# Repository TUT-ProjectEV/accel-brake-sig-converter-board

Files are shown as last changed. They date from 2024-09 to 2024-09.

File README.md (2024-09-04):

# accel-brake-sig-converter-board

## Revision
- v1.0

## Overview
- This board converts the sensor output VOLTAGE signal into the CURRENT signal
    - 4~20mA

## Requirement
### Development
- Kicad 8.0
### Libraries
- ProjectEV-Kicad-Library
    - v8.0

## Usage
- J1, J2, J3: Connect to Controller or ADC and Power supply
    - Pin 1: +12V Input
    - Pin 2: GND
    - Pin 3: Current Signal Output
- J4, J5, J6: Connect to Sensor
    - Pin 1: +5V Output
    - Pin 2: GND
    - Pin 3: Voltage Signal Input

## Features
- Input Signal Voltage Range: +1~+5V
- Output Signal Current Range: 4~20mA
    - 250 Ohms termination: +1~+5V

## Reference
- ["Reference Site Name"]("Reference URL")

## Author
- [ST04-tkmr](https://github.com/ST04-tkmr)

## License
- Copyright (c) 2024 東京工科大学 ProjectEV

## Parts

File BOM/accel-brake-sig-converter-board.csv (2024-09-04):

Reference | Value | Footprint | Qty | DNP | Mouser番号 | Package | digikey品番
C1 | 1000p | ProjectEV_Capacitor:C_3216M | 1 |  |  | 3216M
C2,C3,C4,C5,C6,C7,C8,C9,C10,C11,C12,C13 | 1u | ProjectEV_Capacitor:C_1608M | 12 |  |  | 1608M
C14,C15,C16 | 0.1u | ProjectEV_Capacitor:C_1608M | 3 |  |  | 1608M
C17,C18,C19 | 10n | ProjectEV_Capacitor:C_1608M | 3 | DNP |  | 1608M
D1,D2,D3 | PZ1AH11B-AU_R1_000A1 | ProjectEV_Diode:PZ1AH11B-AU_R1_000A1 | 3 |  | 241-PZ1AH11BAUR1000A
D4,D5,D6,D7,D8,D9 | B1911PG--20D000514U1930 | ProjectEV_LED:B1911PG--20D000514U1930 | 6 |  |  |  | 3147-B1911PG--20D000514U1930CT-ND
F1,F2,F3 | 0ABB-1000-TM | ProjectEV_Fuse:0ABB-1000-TM | 3 |  | 530-0ABB-1000-TM |  | 507-0ABB-5000-TMCT-ND
J1,J2,J3,J4,J5,J6 | SM03B-PASS-TBT | ProjectEV_Connector_JST:SM03B-PASS-TBT | 6 |  |  |  | 455-SM03B-PASS-TBTCT-ND
Q1,Q2,Q3 | DMP3098LQ-7 | ProjectEV_Transistor:DMP3098LQ-7 | 3 |  | 621-DMP3098LQ-7
Q4,Q5,Q6 | 2N7002K-AU_R1_000A2 | ProjectEV_Transistor:2N7002K-AU_R1_000A2 | 3 |  |  |  | 3757-2N7002K-AU_R1_000A2CT-ND
R1 | 1M | ProjectEV_Resistor:R_3216M | 1 |  |  | 3216M
R2,R3 | 0 | ProjectEV_Resistor:R_1608M | 2 |  |  | 1608M
R4,R5,R6,R13,R14,R15,R20,R22,R24,R26,R28,R30,R34,R35,R36 | 100k | ProjectEV_Resistor:R_1608M | 15 |  |  | 1608M
R7,R8,R9,R19,R21,R23,R25,R27,R29 | 10k | ProjectEV_Resistor:R_1608M | 9 |  |  | 1608M
R10,R11,R12 | 100 | ProjectEV_Resistor:R_1608M | 3 |  |  | 1608M
R16,R17,R18 | 3.3k | ProjectEV_Resistor:R_1608M | 3 |  |  | 1608M
R31,R32,R33 | RT1206BRC07250RL | ProjectEV_Resistor:RT1206BRC07250RL | 3 |  | 603-RT1206BRC07250RL | 3216M
U1,U2,U3 | NCV8711BMTW500TBG | ProjectEV_RegulatorLinear:NCV8711BMTW500TBG | 3 |  | 863-NCV8711BMTW500TB
U4,U5,U6 | NCV20072DR2G | ProjectEV_Opamp:NCV20072DR2G | 3 |  | 863-NCV20072DR2G

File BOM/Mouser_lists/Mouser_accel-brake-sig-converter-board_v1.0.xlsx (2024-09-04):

Reference | Manufacturer Part Number | Mouser Part Number | Description | Quantity 1 (実装個数) | Quantity 2
D1,D2,D3 | PZ1AH11B-AU_R1_000A1 | 241-PZ1AH11BAUR1000A |  | 3 | 6
F1,F2,F3 | 0ABB-1000-TM | 530-0ABB-1000-TM |  | 3 | 6
Q1,Q2,Q3 | DMP3098LQ-7 | 621-DMP3098LQ-7 |  | 3 | 6
R31,R32,R33 | RT1206BRC07250RL | 603-RT1206BRC07250RL |  | 3 | 6
U1,U2,U3 | NCV8711BMTW500TBG | 863-NCV8711BMTW500TB |  | 3 | 6

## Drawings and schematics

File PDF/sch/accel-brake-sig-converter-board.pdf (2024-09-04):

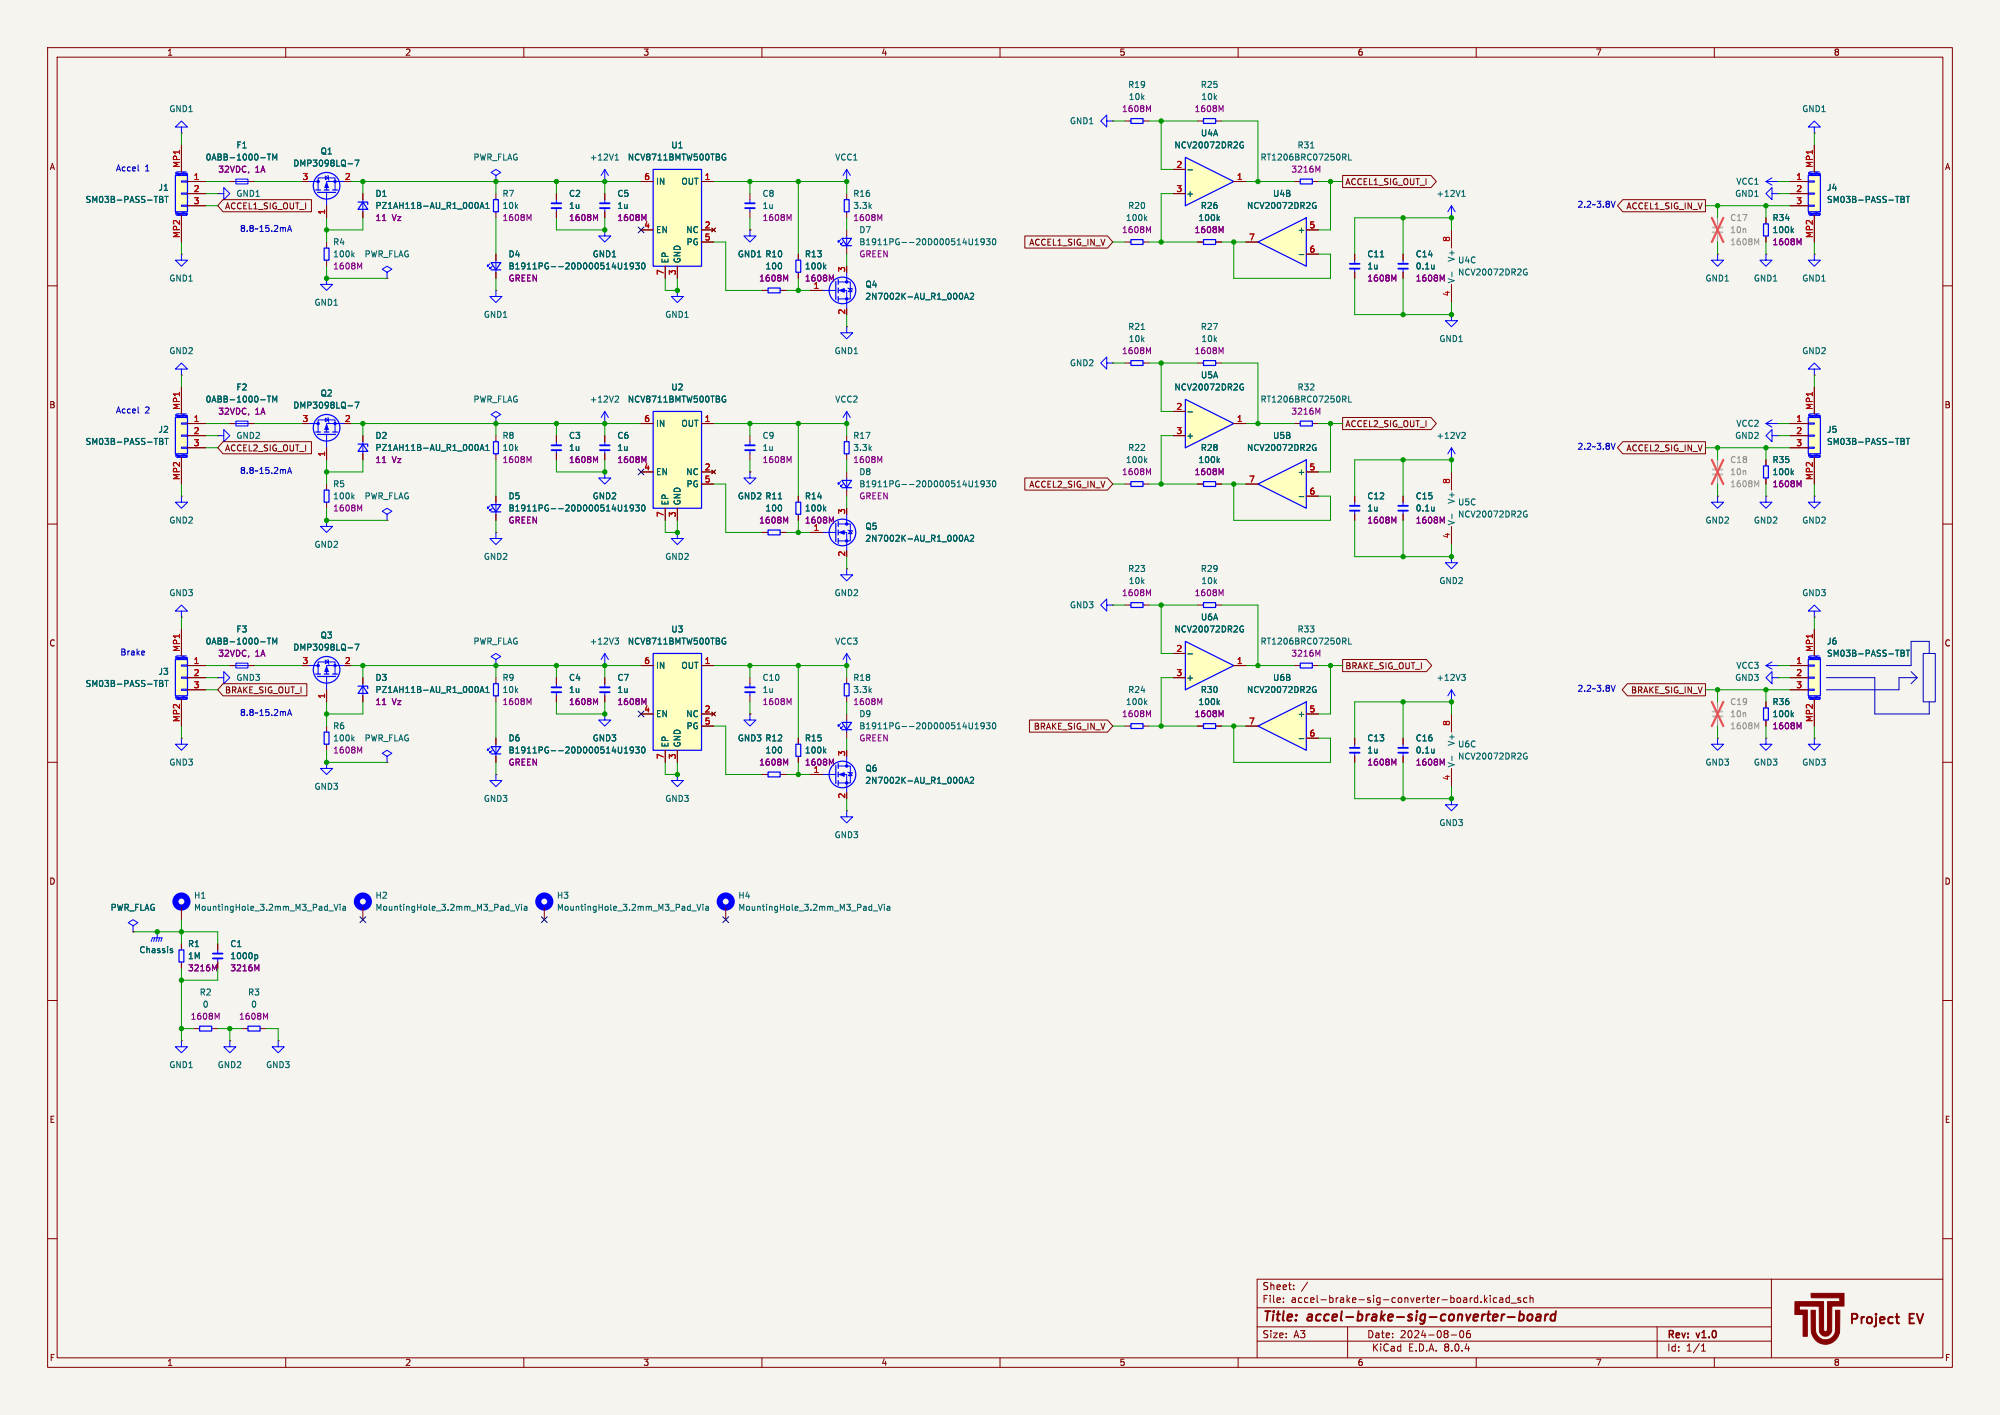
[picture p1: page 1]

Id: 1/1 Title: accel-brake-sig-converter-board

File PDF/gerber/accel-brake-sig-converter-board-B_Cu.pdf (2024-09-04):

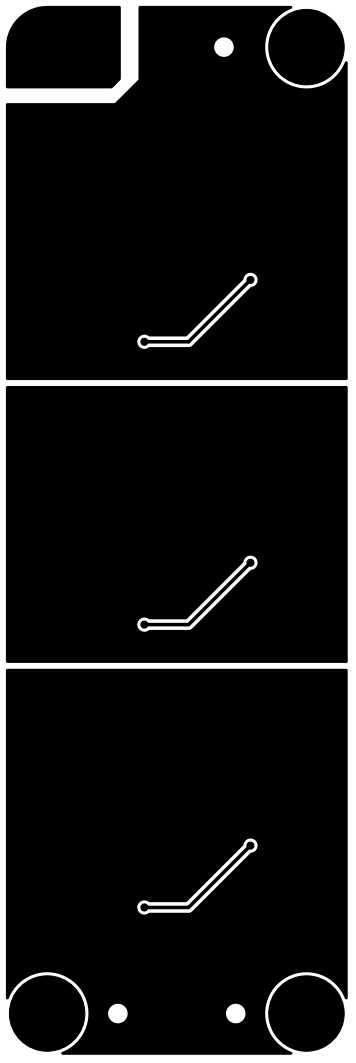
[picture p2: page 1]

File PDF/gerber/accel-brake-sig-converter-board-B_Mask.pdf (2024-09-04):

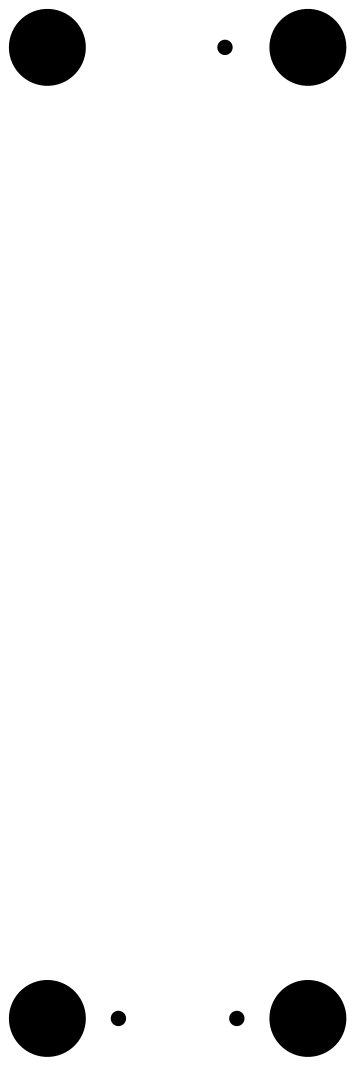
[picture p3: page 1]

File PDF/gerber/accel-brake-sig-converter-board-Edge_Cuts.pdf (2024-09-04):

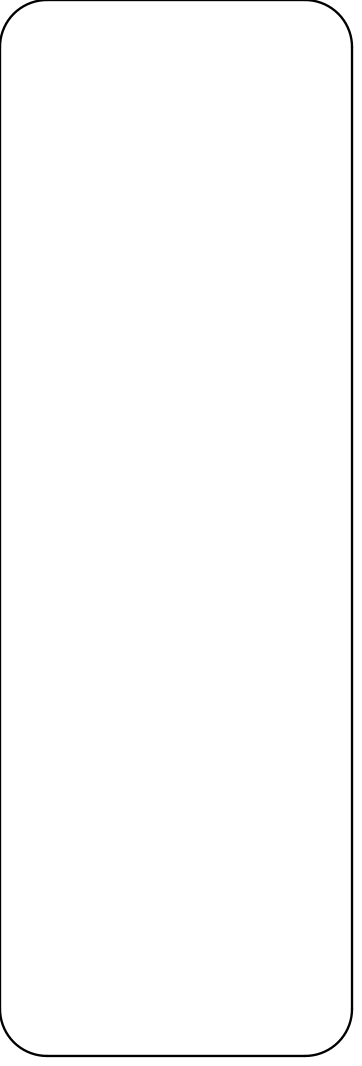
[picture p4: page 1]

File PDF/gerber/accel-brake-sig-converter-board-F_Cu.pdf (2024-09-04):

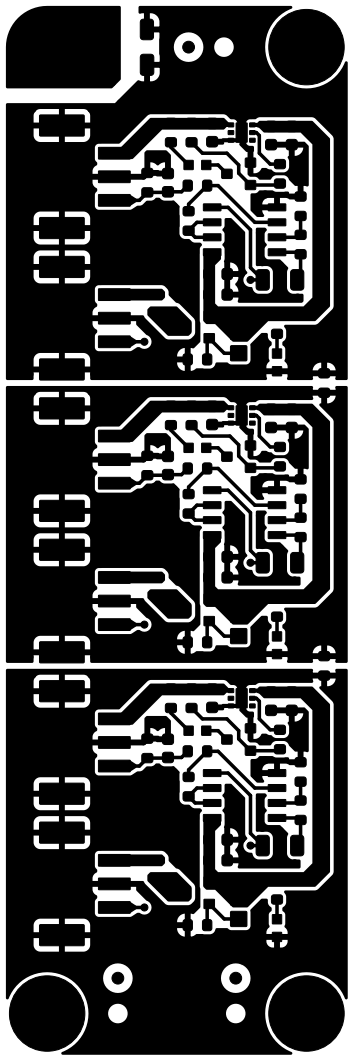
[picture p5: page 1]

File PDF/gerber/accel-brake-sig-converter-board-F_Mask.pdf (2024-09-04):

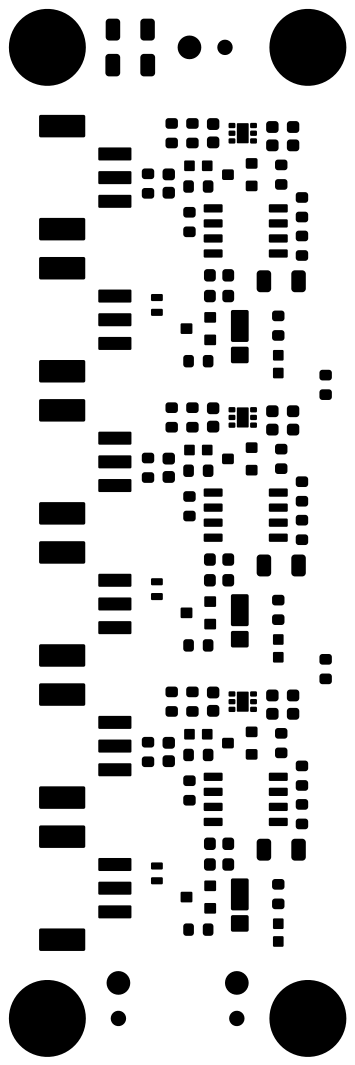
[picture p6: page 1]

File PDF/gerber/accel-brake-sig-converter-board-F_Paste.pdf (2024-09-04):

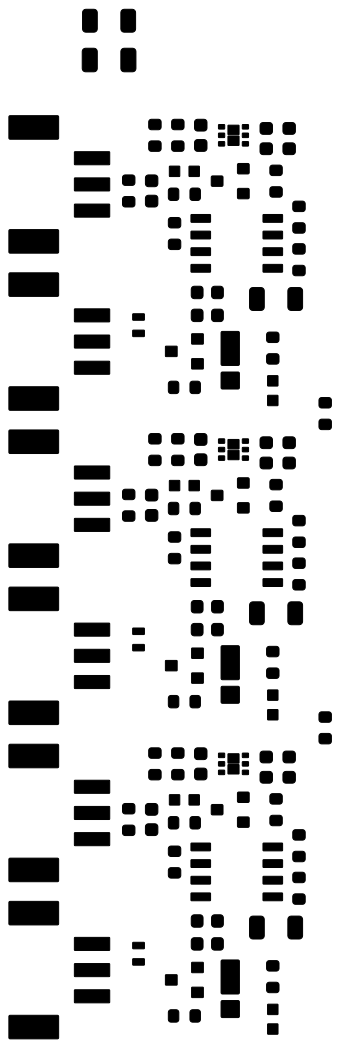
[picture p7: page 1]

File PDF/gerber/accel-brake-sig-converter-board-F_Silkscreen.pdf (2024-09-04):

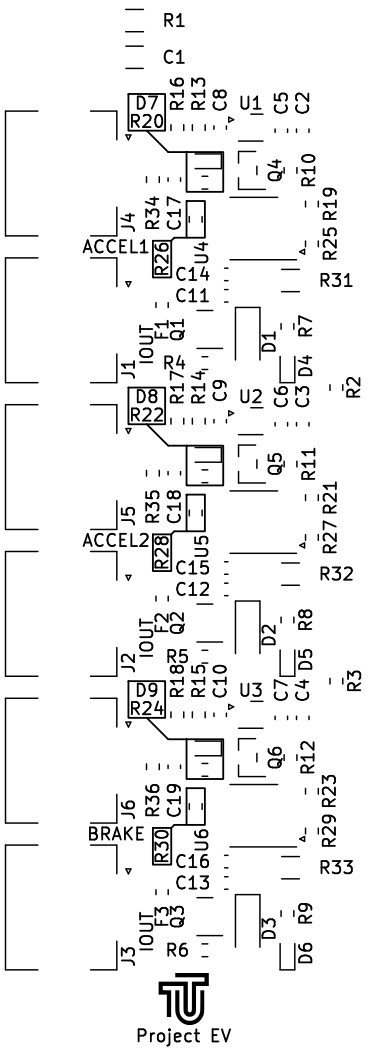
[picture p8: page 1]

IOUT IOUT Project EV

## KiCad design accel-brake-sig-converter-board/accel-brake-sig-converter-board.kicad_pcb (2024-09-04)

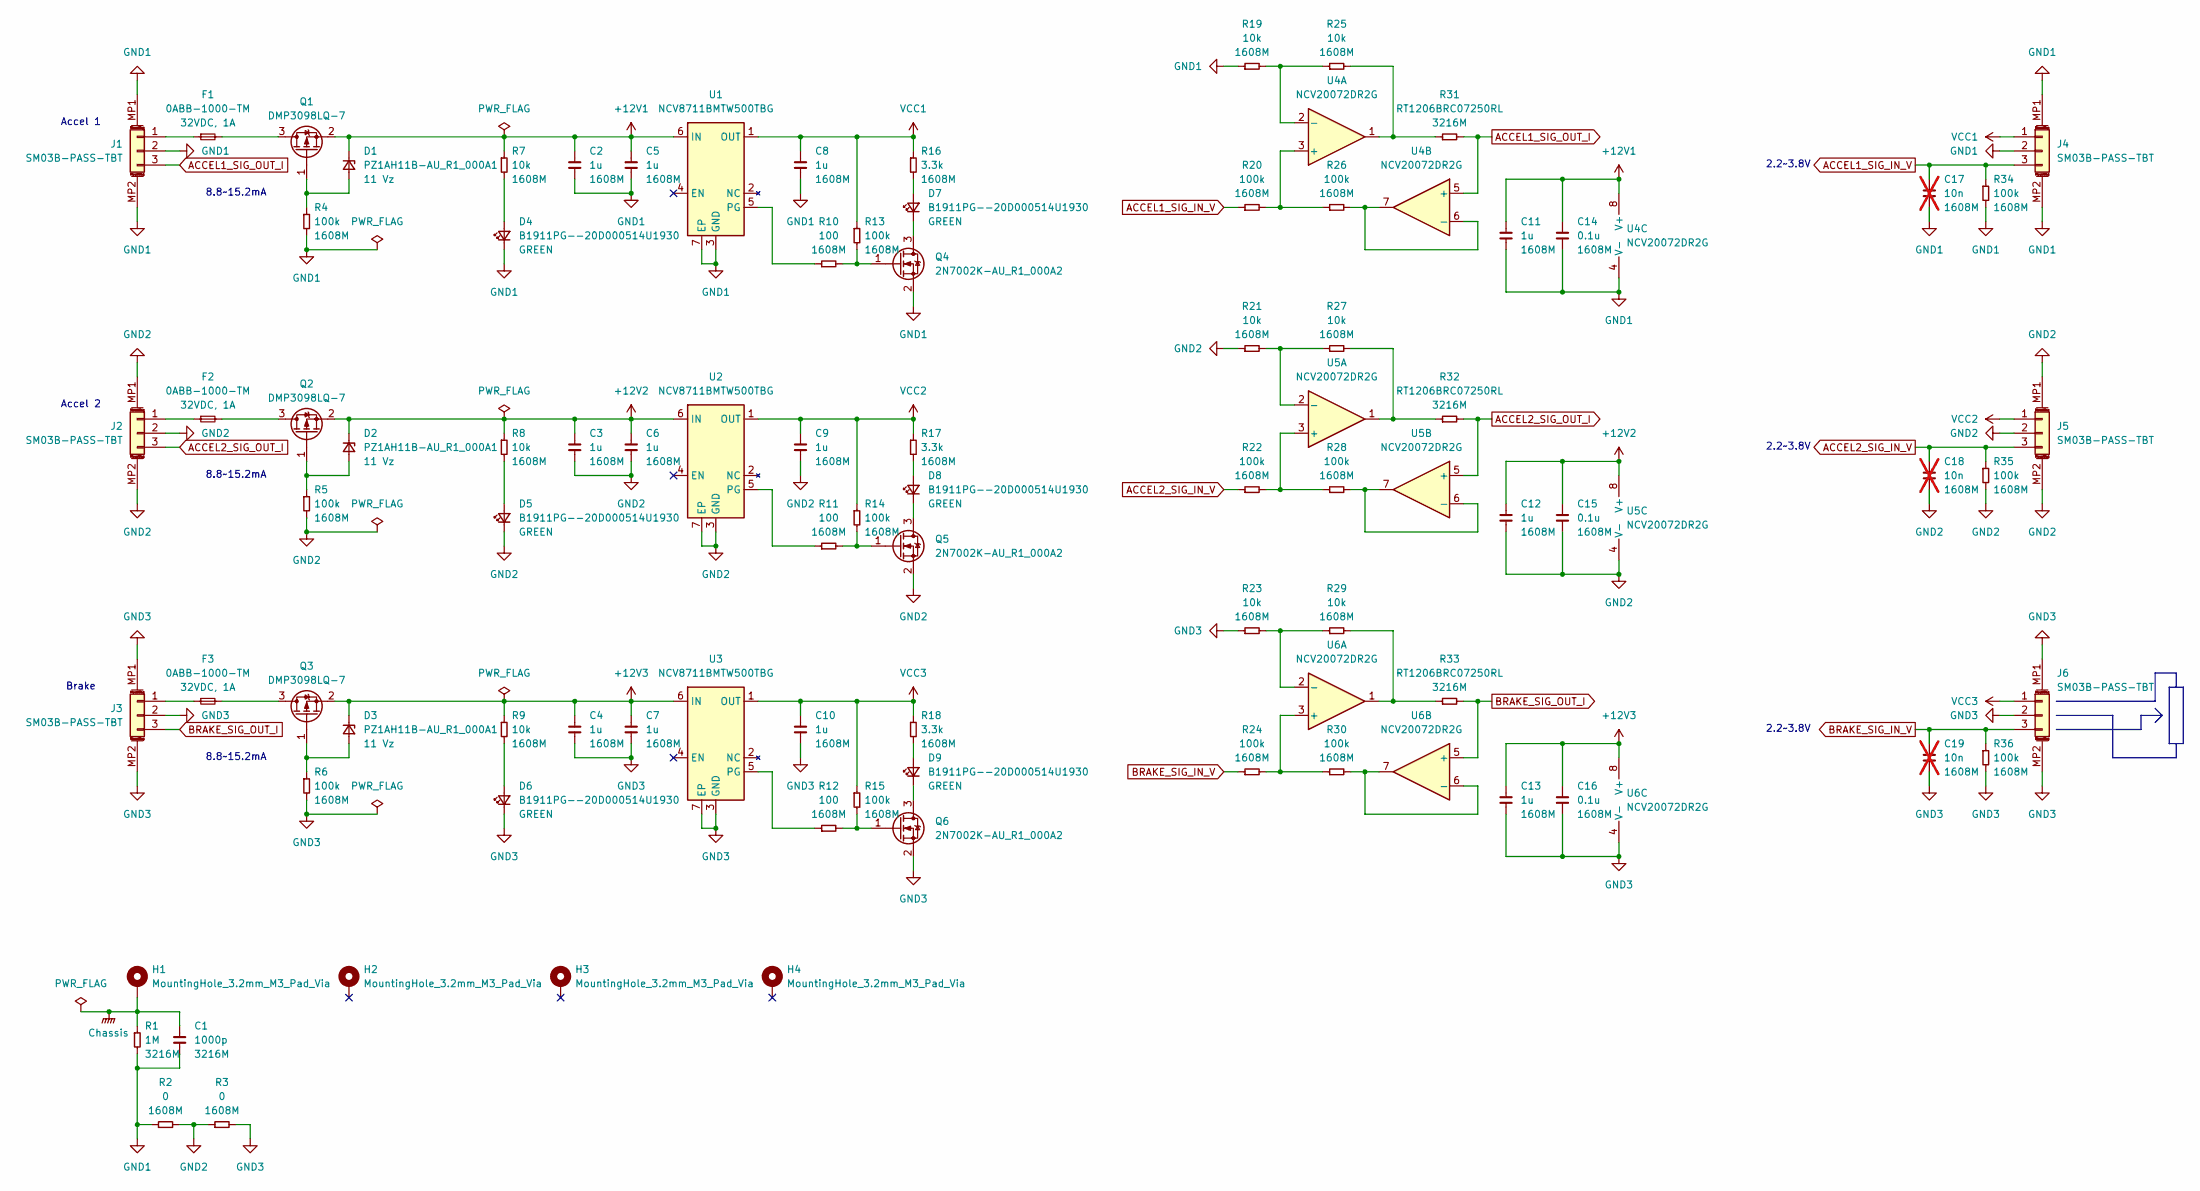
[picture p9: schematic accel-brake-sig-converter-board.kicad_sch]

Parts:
C1: 1000p; C_3216M
C2, C3, C4, C5, C6, C7, C8, C9, C10, C11, C12, C13: 1u; C_1608M
C14, C15, C16: 0.1u; C_1608M
C17, C18, C19: 10n; C_1608M; not fitted
D1, D2, D3: PZ1AH11B-AU_R1_000A1; Mouser番号 241-PZ1AH11BAUR1000A
D4, D5, D6, D7, D8, D9: B1911PG--20D000514U1930; digikey品番 3147-B1911PG--20D000514U1930CT-ND
F1, F2, F3: 0ABB-1000-TM; digikey品番 507-0ABB-5000-TMCT-ND
H1, H2, H3, H4: MountingHole_3.2mm_M3_Pad_Via
J1, J2, J3, J4, J5, J6: SM03B-PASS-TBT; digikey品番 455-SM03B-PASS-TBTCT-ND
Q1, Q2, Q3: DMP3098LQ-7; Mouser番号 621-DMP3098LQ-7
Q4, Q5, Q6: 2N7002K-AU_R1_000A2; digikey品番 3757-2N7002K-AU_R1_000A2CT-ND
R1: 1M; R_3216M
R2, R3: 0; R_1608M
R4, R5, R6, R13, R14, R15, R20, R22, R24, R26, R28, R30, R34, R35, R36: 100k; R_1608M
R7, R8, R9, R19, R21, R23, R25, R27, R29: 10k; R_1608M
R10, R11, R12: 100; R_1608M
R16, R17, R18: 3.3k; R_1608M
R31, R32, R33: RT1206BRC07250RL; Mouser番号 603-RT1206BRC07250RL
U1, U2, U3: NCV8711BMTW500TBG; Mouser番号 863-NCV8711BMTW500TB
U4, U5, U6: NCV20072DR2G; Mouser番号 863-NCV20072DR2G

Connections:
+12V1: C2.1, C5.1, C11.1, C14.1, D1.1 (K), Q1.2 (S), R7.1, U1.6 (IN), U4.8 (V+)
+12V2: C3.1, C6.1, C12.1, C15.1, D2.1 (K), Q2.2 (S), R8.1, U2.6 (IN), U5.8 (V+)
+12V3: C4.1, C7.1, C13.1, C16.1, D3.1 (K), Q3.2 (S), R9.1, U3.6 (IN), U6.8 (V+)
ACCEL1_SIG_IN_V: C17.1, J4.3, R20.1, R34.1
ACCEL1_SIG_OUT_I: J1.3, R31.2, U4.5 (+)
ACCEL2_SIG_IN_V: C18.1, J5.3, R22.1, R35.1
ACCEL2_SIG_OUT_I: J2.3, R32.2, U5.5 (+)
BRAKE_SIG_IN_V: C19.1, J6.3, R24.1, R36.1
BRAKE_SIG_OUT_I: J3.3, R33.2, U6.5 (+)
Chassis: C1.1, H1.MP, R1.1
GND1: C1.2, C2.2, C5.2, C8.2, C11.2, C14.2, C17.2, D4.1 (K), J1.2, J1.MP1 (MountPin), J1.MP2 (MountPin), J4.2, J4.MP1 (MountPin), J4.MP2 (MountPin), Q4.2 (S), R1.2, R2.1, R4.2, R19.1, R34.2, U1.3 (GND), U1.7 (EP), U4.4 (V-)
GND2: C3.2, C6.2, C9.2, C12.2, C15.2, C18.2, D5.1 (K), J2.2, J2.MP1 (MountPin), J2.MP2 (MountPin), J5.2, J5.MP1 (MountPin), J5.MP2 (MountPin), Q5.2 (S), R2.2, R3.1, R5.2, R21.1, R35.2, U2.3 (GND), U2.7 (EP), U5.4 (V-)
GND3: C4.2, C7.2, C10.2, C13.2, C16.2, C19.2, D6.1 (K), J3.2, J3.MP1 (MountPin), J3.MP2 (MountPin), J6.2, J6.MP1 (MountPin), J6.MP2 (MountPin), Q6.2 (S), R3.2, R6.2, R23.1, R36.2, U3.3 (GND), U3.7 (EP), U6.4 (V-)
unnamed: D1.2 (A), Q1.1 (G), R4.1
unnamed: D2.2 (A), Q2.1 (G), R5.1
unnamed: D3.2 (A), Q3.1 (G), R6.1
unnamed: D4.2 (A), R7.2
unnamed: D5.2 (A), R8.2
unnamed: D6.2 (A), R9.2
unnamed: D7.2 (A), R16.2
unnamed: D7.1 (K), Q4.3 (D)
unnamed: D8.2 (A), R17.2
unnamed: D8.1 (K), Q5.3 (D)
unnamed: D9.2 (A), R18.2
unnamed: D9.1 (K), Q6.3 (D)
unnamed: F1.1, J1.1
unnamed: F2.1, J2.1
unnamed: F3.1, J3.1
unnamed: F1.2, Q1.3 (D)
unnamed: F2.2, Q2.3 (D)
unnamed: F3.2, Q3.3 (D)
unnamed: Q4.1 (G), R10.2, R13.2
unnamed: Q5.1 (G), R11.2, R14.2
unnamed: Q6.1 (G), R12.2, R15.2
unnamed: R25.2, R31.1, U4.1
unnamed: R27.2, R32.1, U5.1
unnamed: R29.2, R33.1, U6.1
unnamed: R10.1, U1.5 (PG)
unnamed: R11.1, U2.5 (PG)
unnamed: R12.1, U3.5 (PG)
unnamed: R20.2, R26.1, U4.3 (+)
unnamed: R19.2, R25.1, U4.2 (-)
unnamed: R26.2, U4.6 (-), U4.7
unnamed: R22.2, R28.1, U5.3 (+)
unnamed: R21.2, R27.1, U5.2 (-)
unnamed: R28.2, U5.6 (-), U5.7
unnamed: R24.2, R30.1, U6.3 (+)
unnamed: R23.2, R29.1, U6.2 (-)
unnamed: R30.2, U6.6 (-), U6.7
VCC1: C8.1, J4.1, R13.1, R16.1, U1.1 (OUT)
VCC2: C9.1, J5.1, R14.1, R17.1, U2.1 (OUT)
VCC3: C10.1, J6.1, R15.1, R18.1, U3.1 (OUT)

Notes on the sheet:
Brake
8.8~15.2mA
2.2~3.8V
Accel 1
Accel 2

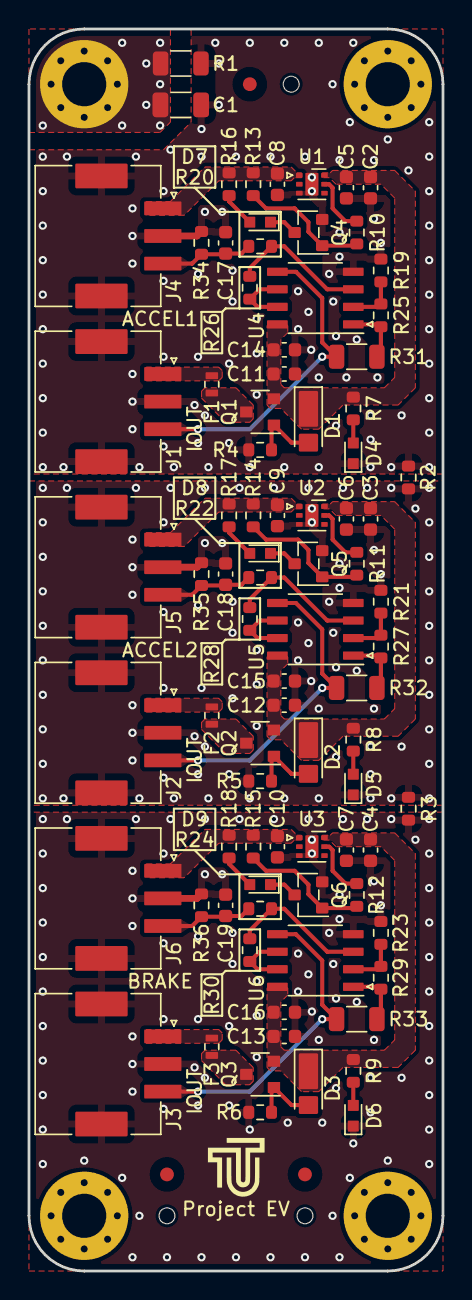
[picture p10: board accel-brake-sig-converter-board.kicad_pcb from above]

Board: 2 copper layers, 30.0 x 90.0 mm, 89 parts (0 on the bottom side), 52 nets.

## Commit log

2024-08-05 create project
    [accel-brake-sig-converter-board.kicad_pcb, accel-brake-sig-converter-board.kicad_sch]
2024-08-05 add title, date, revision
    [accel-brake-sig-converter-board.kicad_sch]
2024-08-08 create sch, add power circuit
    [accel-brake-sig-converter-board.kicad_sch]
2024-08-09 信号処理部追加
    [accel-brake-sig-converter-board.kicad_sch]
2024-08-10 ブレーキセンサ部以外完成
    [accel-brake-sig-converter-board.kicad_sch]
2024-08-12 回路図完成
    [accel-brake-sig-converter-board.kicad_sch]
2024-08-12 update symbol
    [accel-brake-sig-converter-board.kicad_sch]
2024-08-12 素子配置ACCEL1まで
    [accel-brake-sig-converter-board.kicad_pcb]
2024-08-13 配置およそ完了
    [accel-brake-sig-converter-board.kicad_pcb]
2024-08-13 配置完了
    [accel-brake-sig-converter-board.kicad_pcb]
2024-08-14 accel1配線
    [accel-brake-sig-converter-board.kicad_pcb]
2024-08-14 配線完了, DRC完了
    [accel-brake-sig-converter-board.kicad_pcb]
2024-08-14 add fiducials, toolingholes
    [accel-brake-sig-converter-board.kicad_pcb]
2024-08-16 JLCPCB素子選定
    [accel-brake-sig-converter-board.kicad_pcb]
2024-08-16 generate production files by JLCPCB Tools
    [BOM-accel-brake-sig-converter-board.csv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]
2024-08-16 generate pdf of sch, gerber
    [accel-brake-sig-converter-board.kicad_pcb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]
2024-08-18 add JLCPCB PCBA parts list
    [bom.xls]
2024-08-20 add JLCPCB PCBA list
    [bom.xls]
2024-08-20 generate BOM
    [accel-brake-sig-converter-board.csv, accel-brake-sig-converter-board.xlsx]
2024-08-20 create BOM for Mouser
    [Mouser_accel-brake-sig-converter-board_v1.0.xlsx]
2024-09-04 README.md を更新
